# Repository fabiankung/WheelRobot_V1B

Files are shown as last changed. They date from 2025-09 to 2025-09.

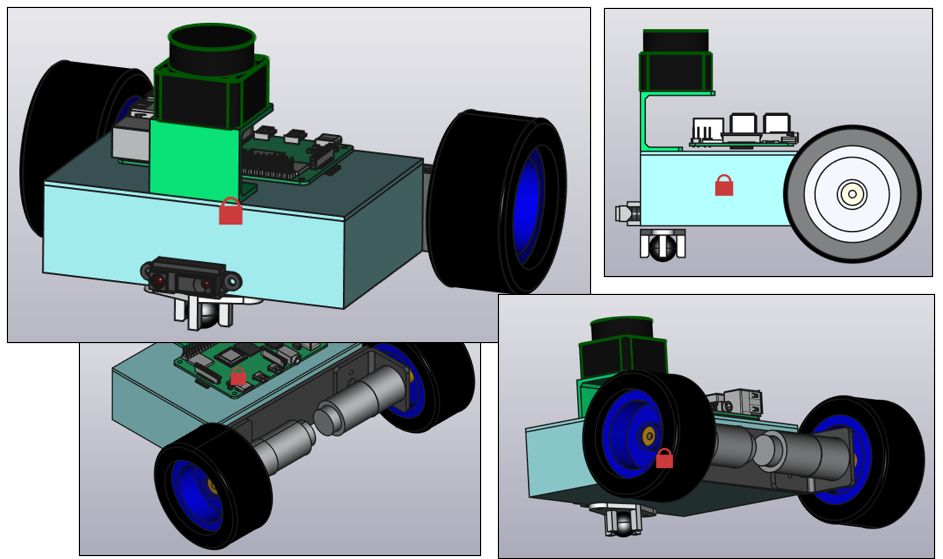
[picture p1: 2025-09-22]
WR1B.jpg

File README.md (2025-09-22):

# WheelRobot_V1B
A simple wheel robot using differential drive locomotion, with Raspberry Pi 4B single-board computer running ROS2 middleware for high-level control and monitoring. The robot has a custom low-level robot controller board using the chip dsPIC33CK512MP606 as the processor for controlling the DC motors and interfacing with on-board sensors. See the PDF file in this repo for the details of the low-level robot controller.

For videos of the robot in action, please see: https://youtu.be/-Cyti25GG1c

WR1B





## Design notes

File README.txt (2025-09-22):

The Sharp IR sensor CAD model is imported from STEP file, courtesy of DonLabs: https://grabcad.com/library/sharp-ir-sensor-gp2y0a41sk0f-1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,and%20also%20the%20data%20sheet%20for%20reference. 

The FreeCAD model for Raspberry Pi 4 is courtesy of rottengetter: https://forum.freecad.org/viewtopic.php?t=59273

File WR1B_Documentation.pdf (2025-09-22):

# CAD Design Using FreeCAD V1.0.0

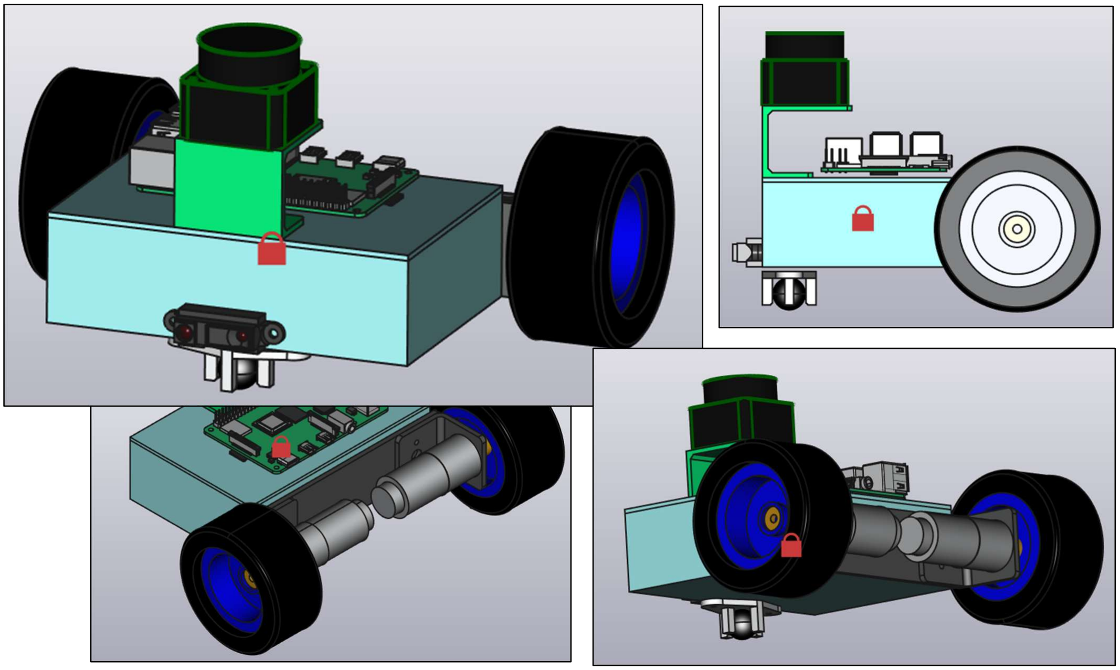
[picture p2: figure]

Wheel Robot Platform | 2025 by Fabian Kung Wai Lee | 1

# Wheel Robot Platform – WR1B

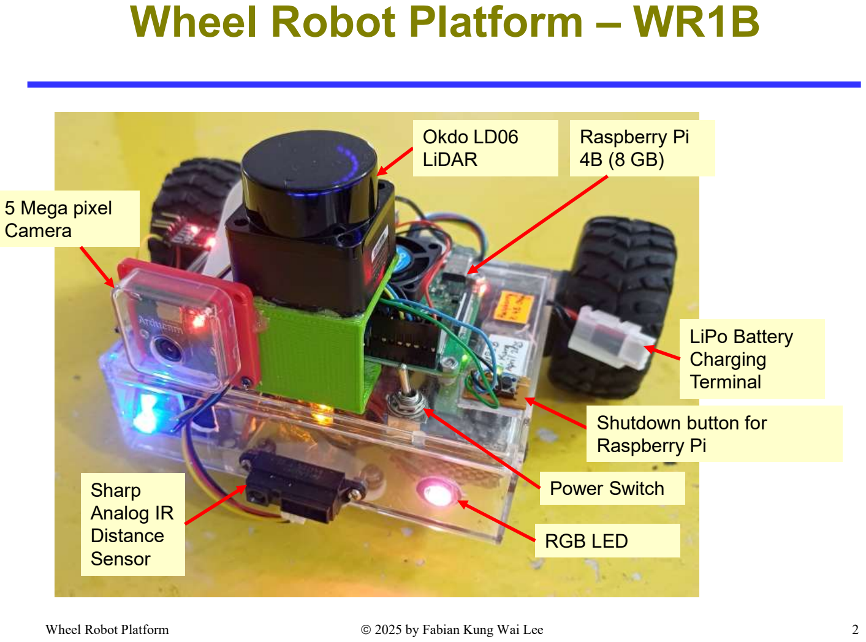
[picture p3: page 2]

Wheel Robot Platform | 2025 by Fabian Kung Wai Lee | 2

# Sharp Analog IR Distance Sensor

# Okdo LD06 LiDAR

# Raspberry Pi 4B (8 GB)

# 5 Mega pixel Camera

# RGB LED

# Power Switch

# LiPo Battery Charging Terminal

# Shutdown button for Raspberry Pi

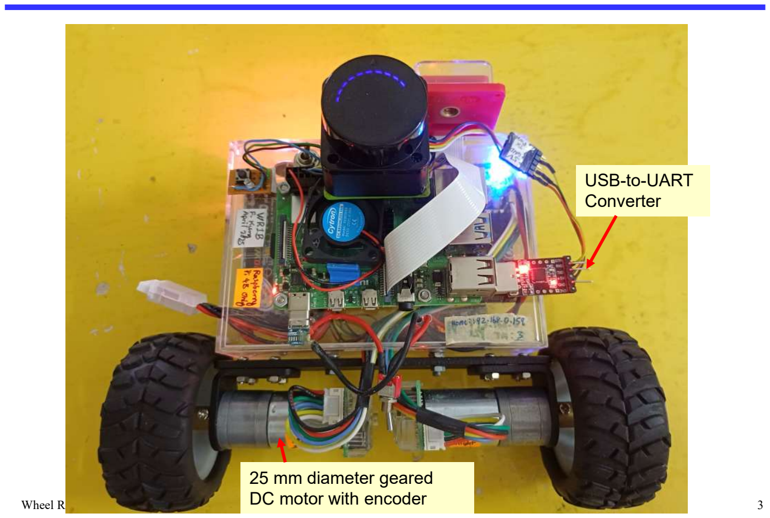
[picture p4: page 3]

Wheel Robot Platform | 2025 by Fabian Kung Wai Lee | 3

# 25 mm diameter geared DC motor with encoder

# USB-to-UART Converter

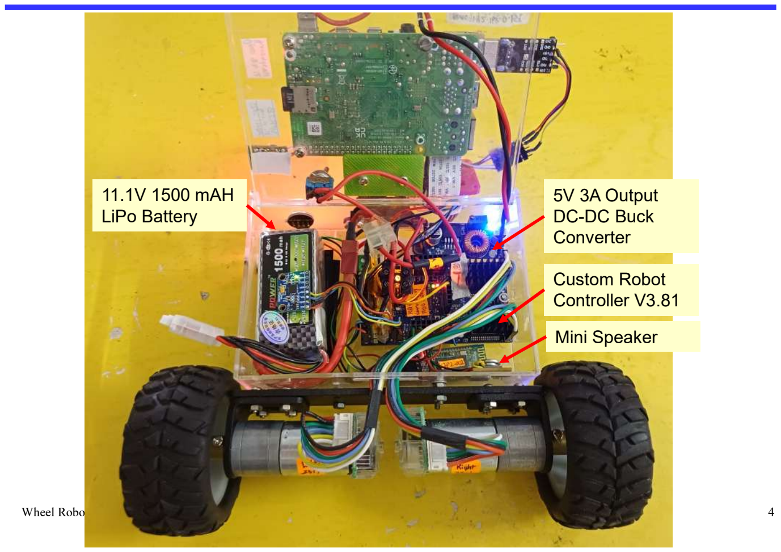
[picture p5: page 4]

Wheel Robot Platform | 2025 by Fabian Kung Wai Lee | 4

# 11.1V 1500 mAH LiPo Battery

# 5V 3A Output DC-DC Buck Converter

# Custom Robot Controller V3.81

# Mini Speaker

# Schematic of Robot Controller (V3.81) – MCU Core

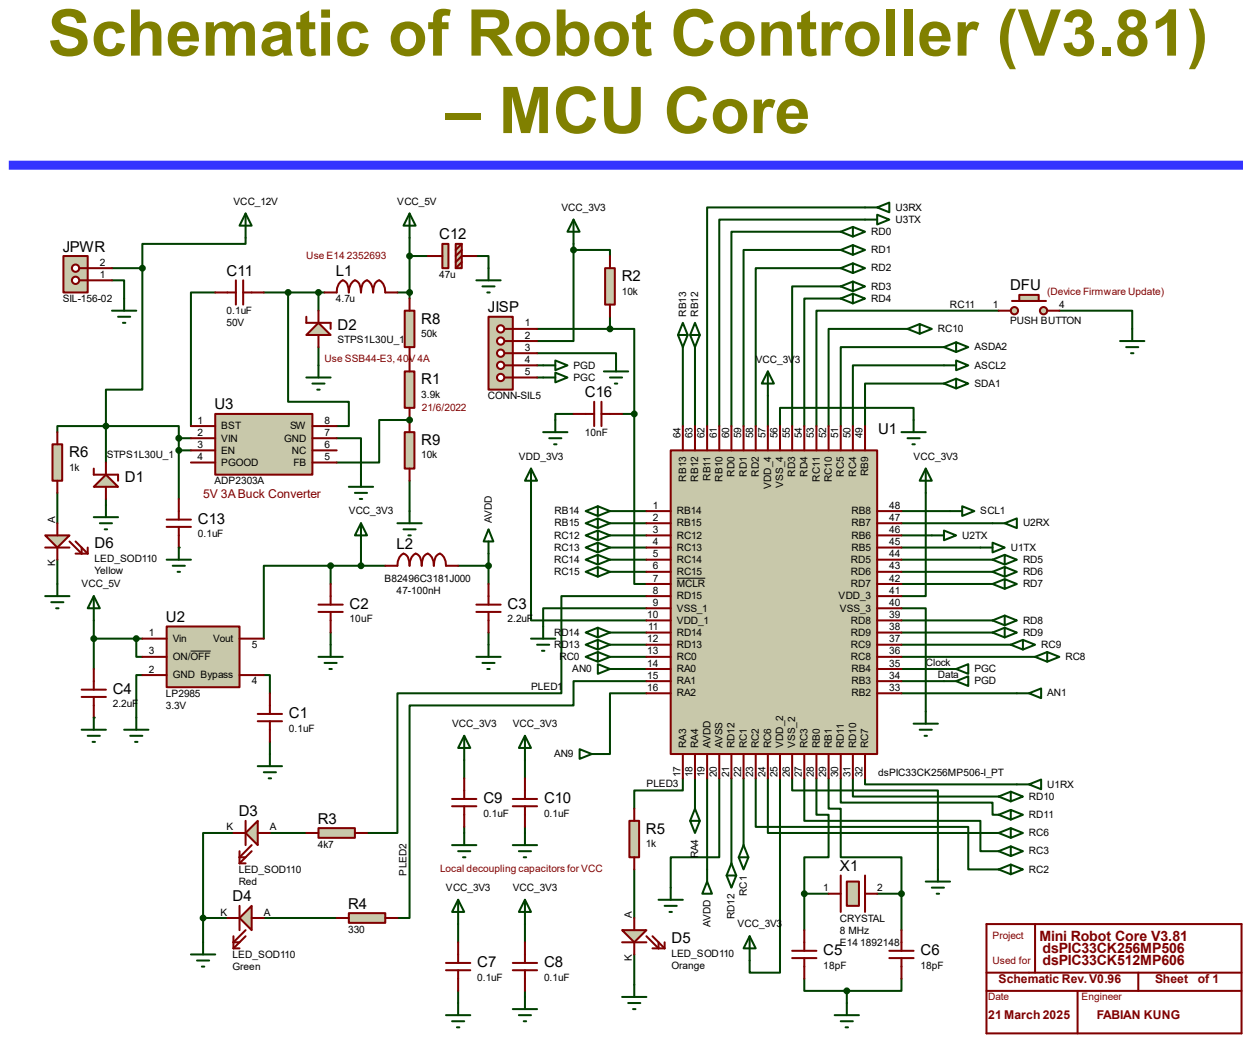
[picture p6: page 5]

Local decoupling capacitors for VCC
VCC_3V3

Project Used for | Mini Robot Core V3.81 dsPIC33CK512MP606 dsPIC33CK256MP506

Schematic Rev. V0.96 | Sheet of 1
Date 21 March 2025 | Engineer FABIAN KUNG

# Schematic of Robot Controller (V3.81) – I/O Ports Connections

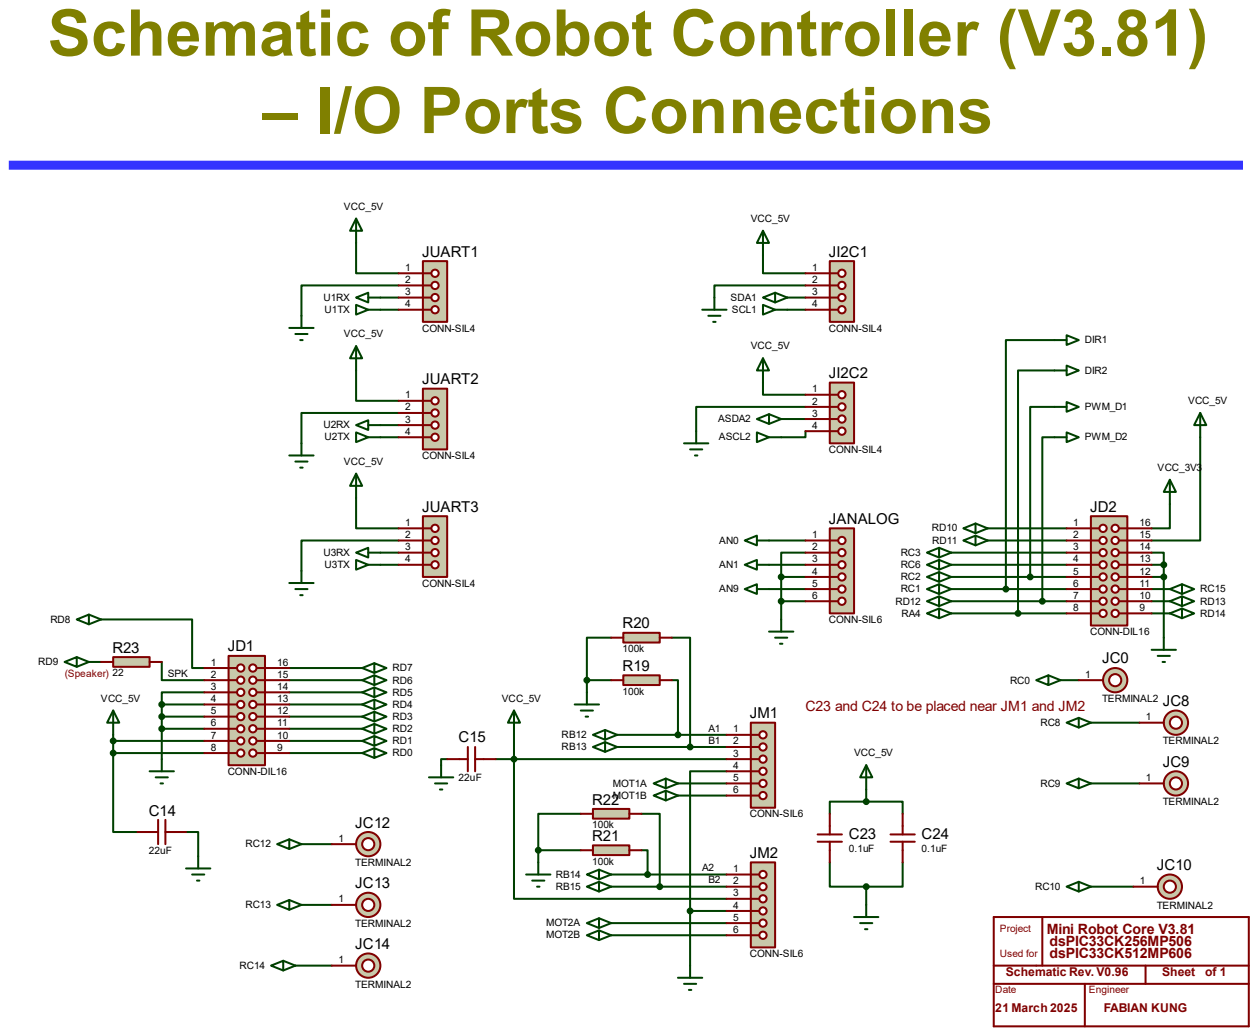
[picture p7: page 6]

C23 and C24 to be placed near JM1 and JM2

Project Used for | Mini Robot Core V3.81 dsPIC33CK512MP606 dsPIC33CK256MP506

Schematic Rev. V0.96 | Sheet of 1
Date 21 March 2025 | Engineer FABIAN KUNG

# Schematic of Robot Controller (V3.81) – Dual DC Motors Driver

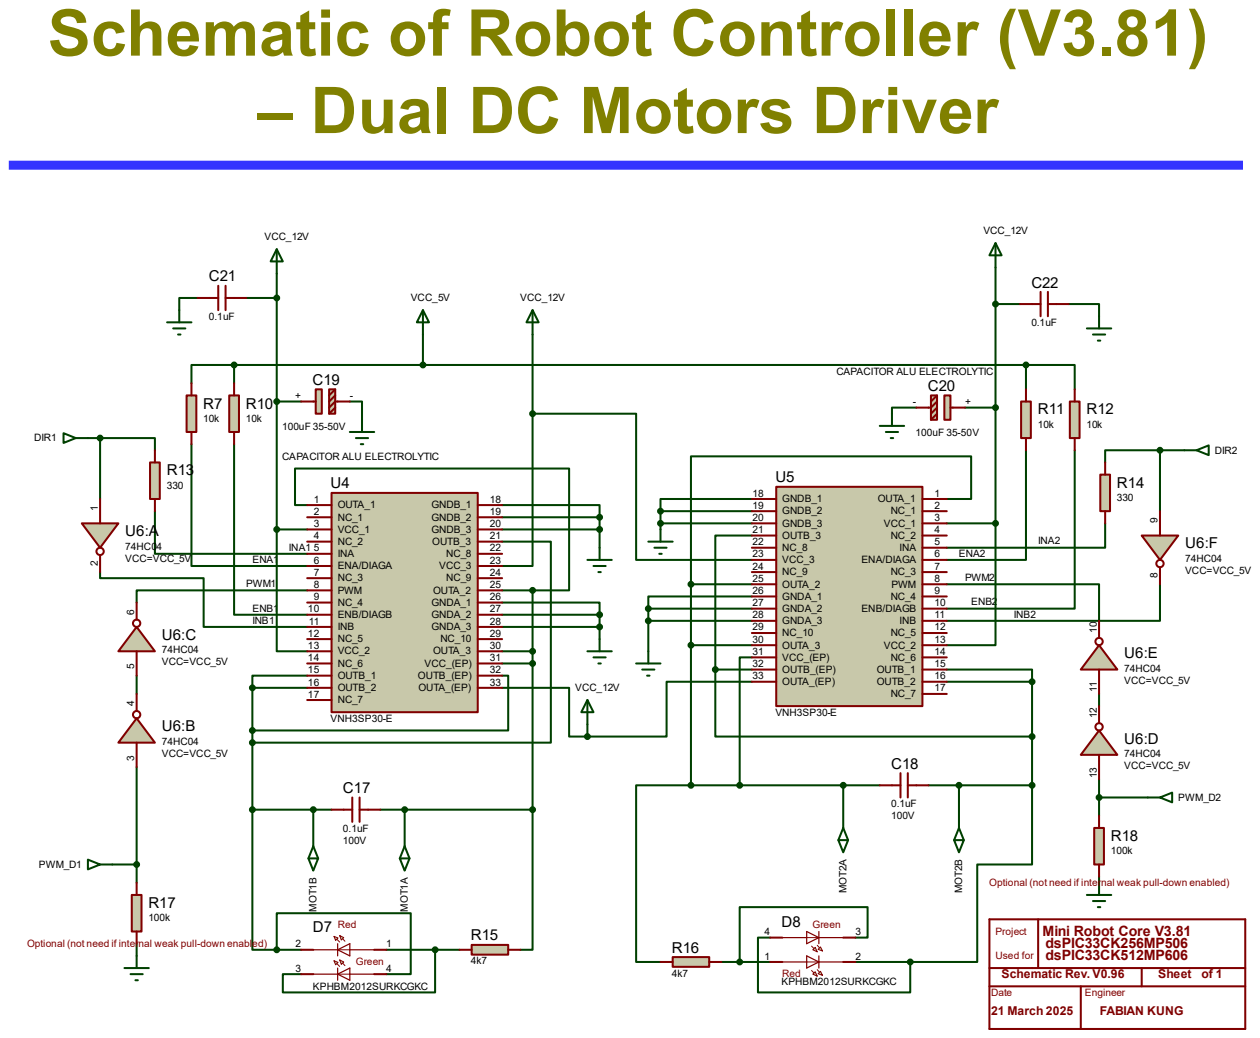
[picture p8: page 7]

100k Optional (not need if internal weak pull-down enabled)
PWM_D1

Optional (not need if internal weak pull-down enabled)

Project Used for | Mini Robot Core V3.81 dsPIC33CK512MP606 dsPIC33CK256MP506

Schematic Rev. V0.96 | Sheet of 1
Date 21 March 2025 | Engineer FABIAN KUNG

# PCB Artwork of Robot Controller

(V3.81)

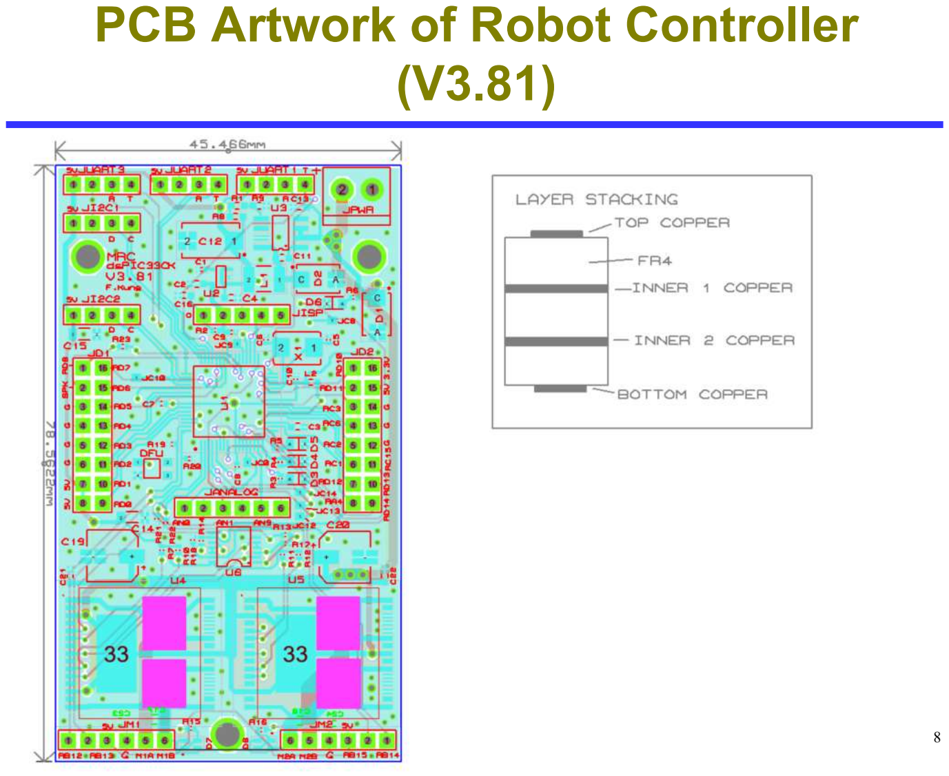
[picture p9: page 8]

Wheel Robot Platform | 2025 by Fabian Kung Wai Lee | 8

# Wiring Diagram

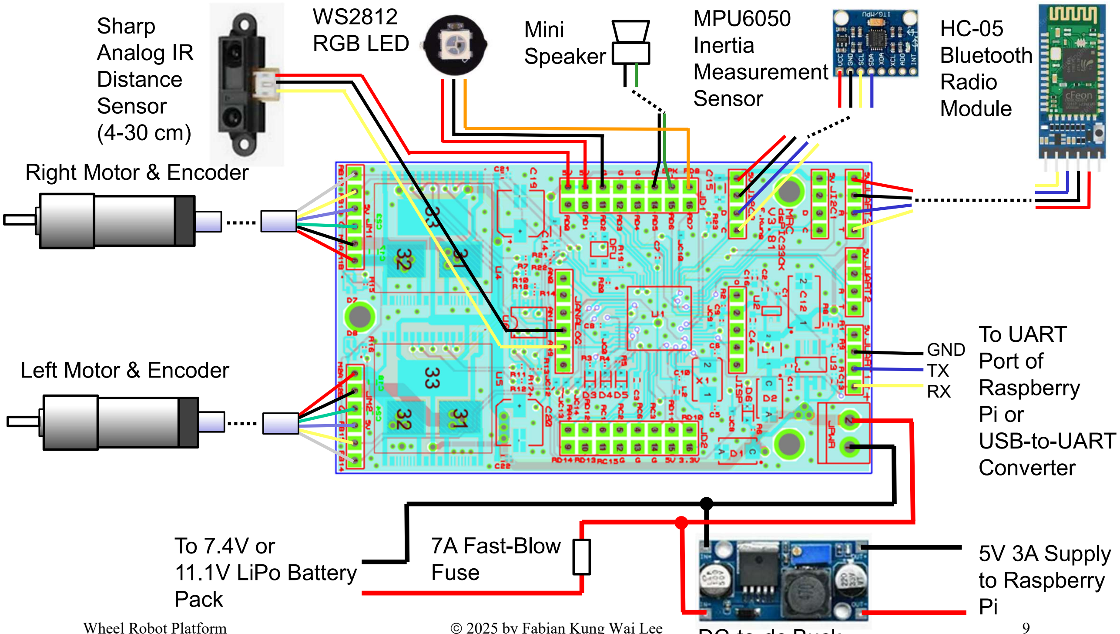
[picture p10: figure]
Right Motor & Encoder; Left Motor & Encoder; GND TX RX; HC-05 Bluetooth Radio Module; MPU6050 Inertia Measurement Sensor; To UART Port of Raspberry Pi or USB-to-UART Converter; To 7.4V or 11.1V LiPo Battery Pack; 5V 3A Supply to Raspberry Pi; 7A Fast-Blow Fuse; RGB LED; Mini; Speaker; Sharp Analog IR Distance Sensor (4-30 cm)

Wheel Robot Platform | 2025 by Fabian Kung Wai Lee | 9

# DC-to-dc Buck Converter

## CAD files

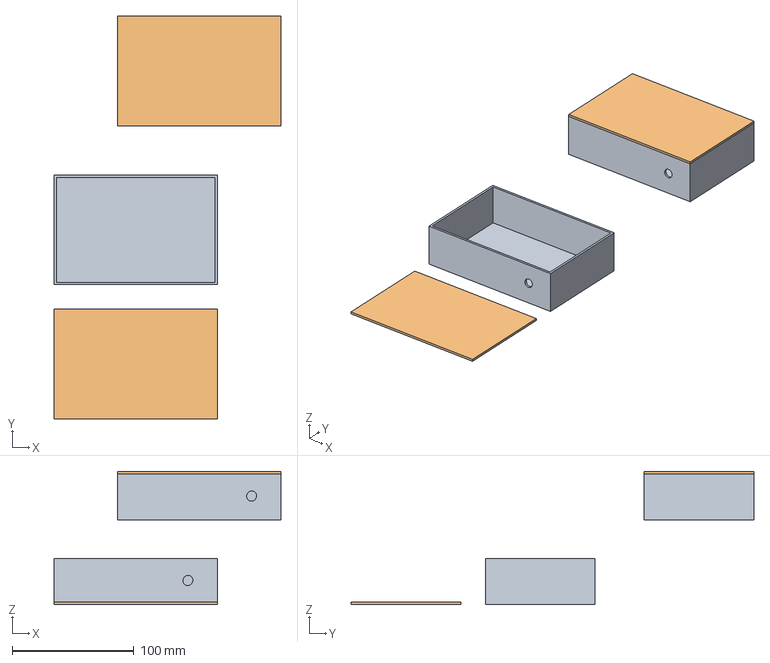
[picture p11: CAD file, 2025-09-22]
Mechanical_CAD/Main_Enclosure.FCStd
186.3 x 330.3 x 109.4 mm
Body_Bottom x 2
Body_Top x 2

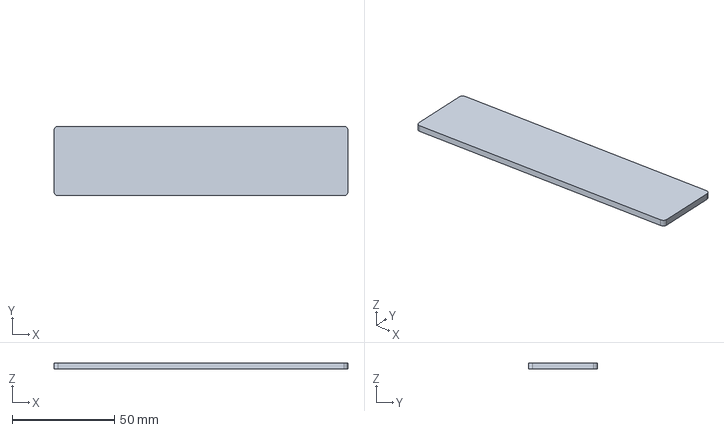
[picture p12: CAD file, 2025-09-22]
Mechanical_CAD/Motor_Sub_Assembly_Bracket.FCStd
144.0 x 34.0 x 3.00 mm

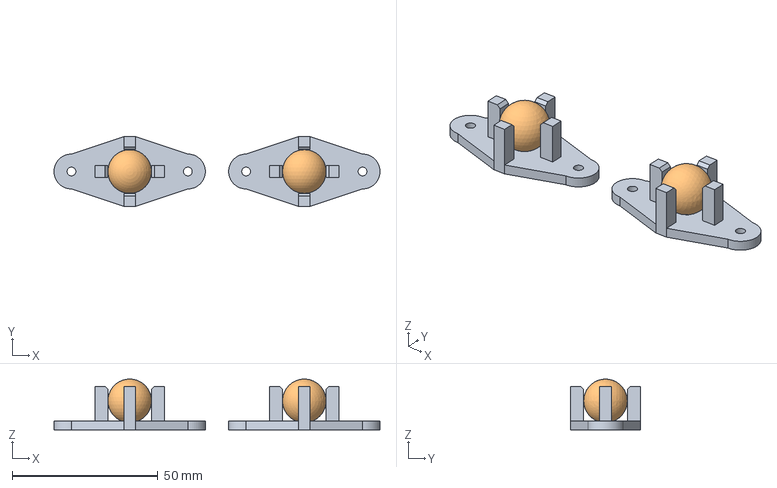
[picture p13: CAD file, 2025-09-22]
Mechanical_CAD/Castor_W420_Steel_Ball.FCStd
112.0 x 24.0 x 17.5 mm
Plastic_Bracket x 2
Steel_Ball x 2

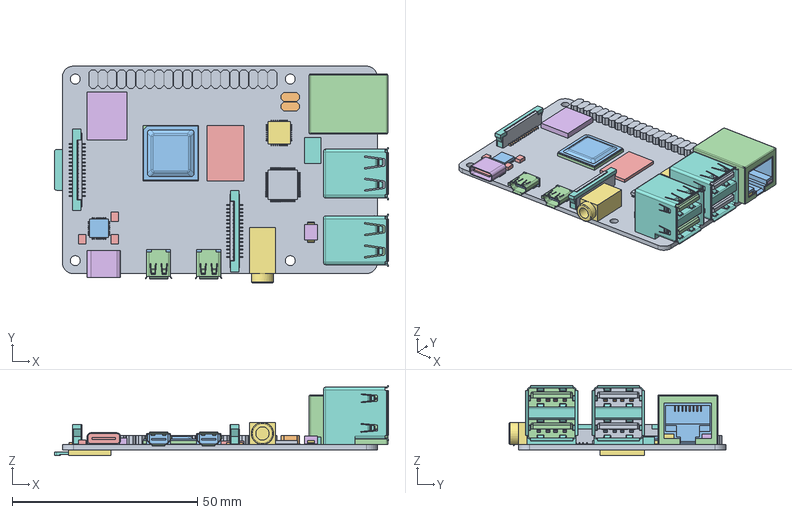
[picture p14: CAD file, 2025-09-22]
Mechanical_CAD/RaspPi-4B_rottengatter.FCStd
90.1 x 58.5 x 19.0 mm
PCB
Chip Carrier
Heat Spreader
Solder
RAM (LPDDR4)
Radio
Package x 3
Pins x 6
Inductor x 3
Capacitor
Shield x 6
Network Wires
LED (yellow)
LED (green)
Pin Carrier x 2
Pins (Upper Connector) x 2
Pins (Lower Connector) x 2
Phone Socket (Audio/Video)
Holder x 2
SD Card Slot
Contacts

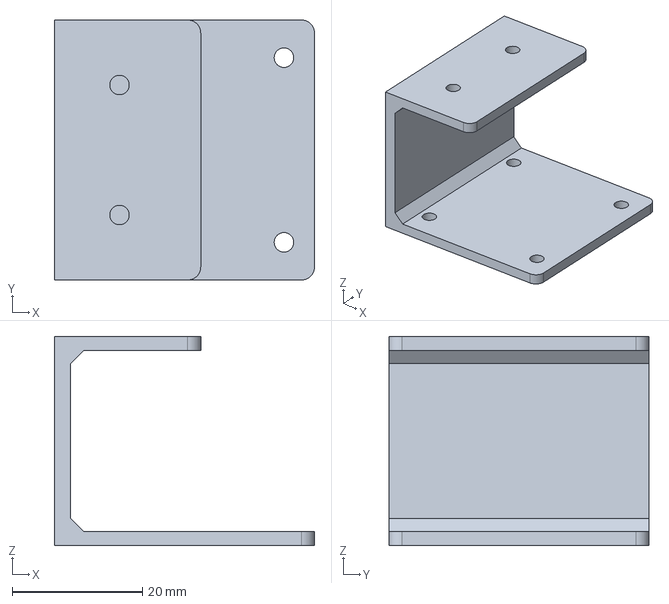
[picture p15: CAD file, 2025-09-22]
Mechanical_CAD/Lidar_Bracket.FCStd
40.0 x 40.0 x 32.2 mm

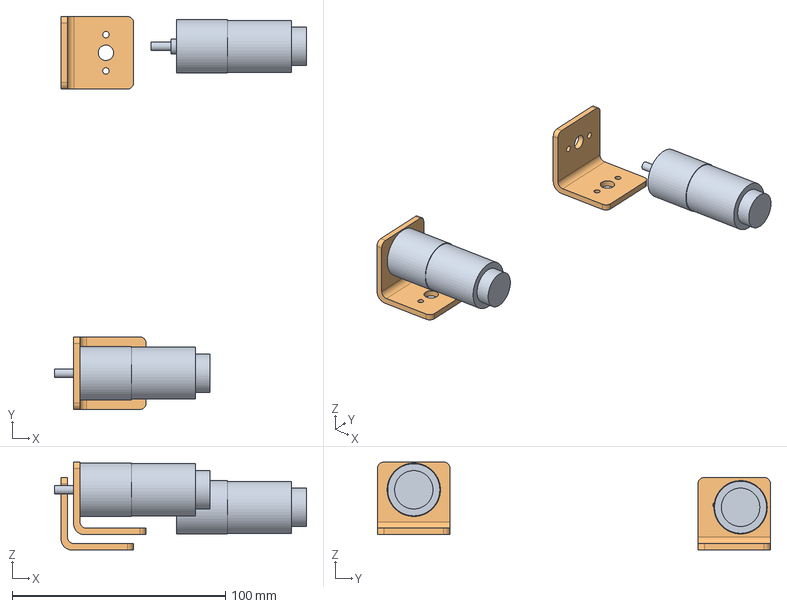
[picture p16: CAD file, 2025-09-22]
Mechanical_CAD/JGA25_DCMotor.FCStd
118.1 x 184.1 x 41.2 mm
Motor_Assembly x 2
Bracket x 2

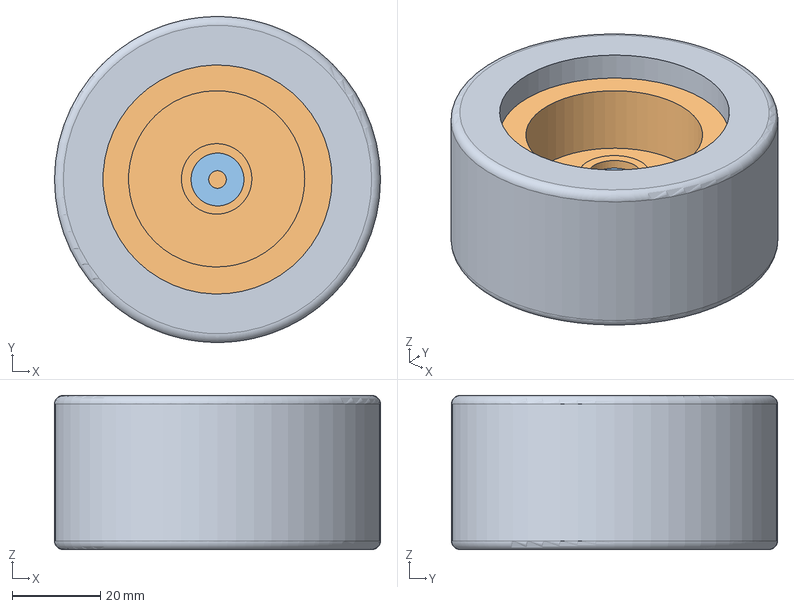
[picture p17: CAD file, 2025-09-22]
Mechanical_CAD/RubberWheel_75mm.FCStd
74.0 x 74.0 x 35.0 mm
Outer_Rubber
Rim
Coupler

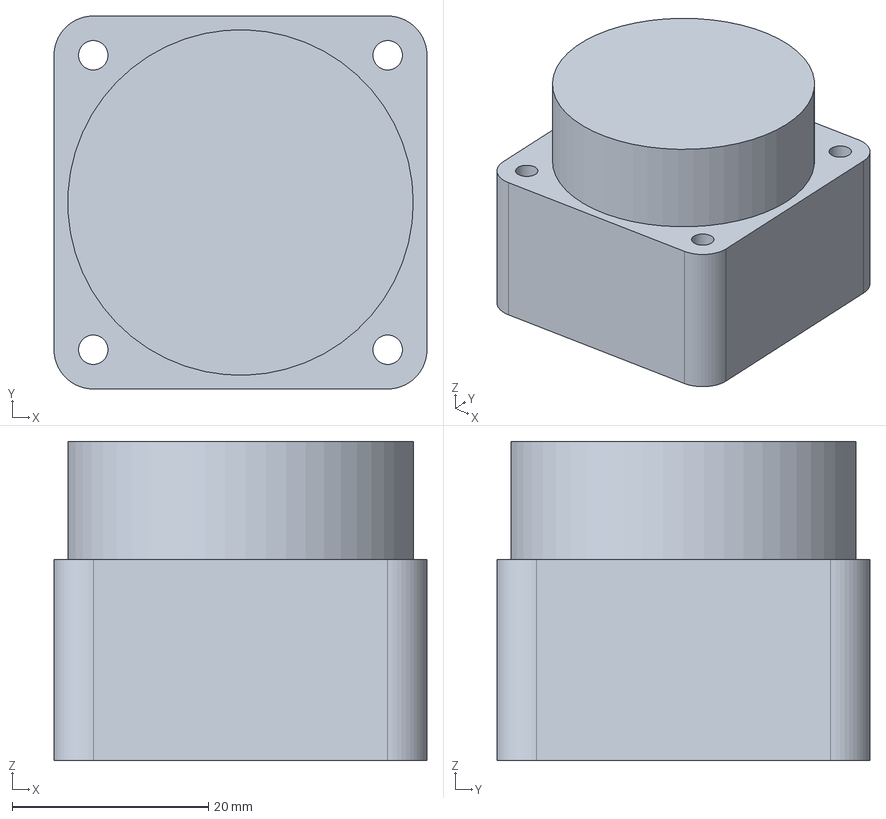
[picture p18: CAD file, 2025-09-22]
Mechanical_CAD/Lidar_Okdo_LD02.FCStd
38.0 x 38.0 x 32.5 mm

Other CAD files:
Mechanical_CAD/Assembly/WR1B.FCStd

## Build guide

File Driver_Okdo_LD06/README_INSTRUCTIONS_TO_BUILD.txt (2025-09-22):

1. Create a workspace in your home folder, say ros2_linolidar_ws.
2. Create a sub-folder /src in your workspace.
3. Copy the folder ldlidar into /src.
4. Goto your workspace in a terminal, i.e. /ros2_linolidar_ws
5. Build the project by running 'colcon build'

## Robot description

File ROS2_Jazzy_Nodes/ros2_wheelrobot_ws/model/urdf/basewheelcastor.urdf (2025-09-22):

<?xml version="1.0"?>
<robot name="fk_wheelrobot">

    <material name="grey">
        <color rgba="0.5 0.5 0.5 1" />
    </material>

    <material name="blue">
        <color rgba="0 0 0.5 1" />
    </material>
    
    <material name="lightgrey">
        <color rgba="0.8 0.8 0.8 1" />
    </material>    
    
    <material name="darkgrey">
        <color rgba="0.2 0.2 0.2 1" />
    </material>       
     
    <material name="white">
        <color rgba="1 1 1 1" />
    </material>      
    
    <!-- base_link (required for Nav2) -->
    <link name="base_link">
        <visual>
            <geometry>
                <box size="0.145 0.1 0.085" />
            </geometry>
            <origin xyz="0 0 0" rpy="0 0 0" />
            <material name="blue" />
        </visual>
    </link>
    
    <!-- base_footprint (projection of base_link on the ground) -->
    <!-- Required for Nav2 and Rviz2 -->
    <link name="base_footprint"/>   
    
    <joint name="base_joint" type="fixed">
        <parent link="base_footprint"/>
        <child link="base_link"/>
        <origin xyz="0 0 0.0645" rpy="0 0 0"/>
    </joint>    
     
    <!-- Wheels (2 differential wheels) -->

    <link name="left_wheel">
        <visual>
            <geometry>
                <cylinder radius="0.04" length="0.0385"/>
            </geometry>
            <origin xyz="0 0 0" rpy="1.57 0 0" />
            <material name="darkgrey" />
        </visual>
    </link>
    <joint name="base_left_wheel_joint" type="continuous">
        <parent link="base_link"/>
        <child link="left_wheel"/>
        <origin xyz="-0.0425 0.075 -0.0245" rpy="0 0 0"/>
        <axis xyz="0 1 0"/>
    </joint>
        
    <link name="right_wheel">
        <visual>
            <geometry>
                <cylinder radius="0.04" length="0.0385"/>
            </geometry>
            <origin xyz="0 0 0" rpy="1.57 0 0" />
            <material name="darkgrey" />
        </visual>
    </link>     
    <joint name="base_right_wheel_joint" type="continuous">
        <parent link="base_link"/>
        <child link="right_wheel"/>
        <origin xyz="-0.0425 -0.075 -0.0245" rpy="0 0 0"/>
        <axis xyz="0 1 0"/>
    </joint>
    
    <!-- Castor wheel to keep the balance -->
    <link name="caster_wheel">
        <visual>
            <geometry>
                <sphere radius="0.011"/>
            </geometry>
            <origin xyz="0 0 0" rpy="0 0 0" />
            <material name="white" />
        </visual>
    </link>  
    
    <joint name="base_caster_wheel_joint" type="fixed">
        <parent link="base_link"/>
        <child link="caster_wheel"/>
        <origin xyz="0.0525 0 -0.054" rpy="0 0 0"/>
    </joint>  
             
</robot>

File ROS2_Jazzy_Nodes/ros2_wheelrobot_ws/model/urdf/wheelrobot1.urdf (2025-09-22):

<?xml version="1.0"?>

<!-- Last modified 11 Aug 2025 -->
<!-- by Fabian Kung -->

<robot name="fk_wheelrobot" xmlns:xacro="http://ros.org/wiki/xacro">

    <material name="grey">
        <color rgba="0.5 0.5 0.5 1" />
    </material>

    <material name="blue">
        <color rgba="0 0 0.5 1" />
    </material>
    
    <material name="lightgrey">
        <color rgba="0.8 0.8 0.8 1" />
    </material>    
    
    <material name="darkgrey">
        <color rgba="0.2 0.2 0.2 1" />
    </material>       
     
    <material name="white">
        <color rgba="1 1 1 1" />
    </material> 
    
    <material name="yellow">
        <color rgba="1 1 0 1" />
    </material>      
    
    <!-- base_link (required for Nav2) -->
    <link name="base_link">
        <visual>
            <geometry>
                <box size="0.145 0.1 0.085" />
            </geometry>
            <origin xyz="0 0 0" rpy="0 0 0" />
            <material name="blue" />
        </visual>
    </link>
    
    <!-- base_footprint (projection of base_link on the ground) -->
    <!-- Required for Nav2 and Rviz2 -->
    <link name="base_footprint"/>   
    
    <joint name="base_joint" type="fixed">
        <parent link="base_footprint"/>
        <child link="base_link"/>
        <origin xyz="0 0 0.0645" rpy="0 0 0"/>
    </joint>    
     
   <!-- Top_body -->
    <link name="top_link">
        <visual>
            <geometry>
                <box size="0.132 0.160 0.028" />
            </geometry>
            <origin xyz="0 0 0" rpy="0 0 0" />
            <material name="blue" />
        </visual>
    </link>  
    
    <!-- The z offset is 0.5*(base_link.height + top_link.height)-->
    <joint name="base_top_joint" type="fixed">
        <parent link="base_link"/>
        <child link="top_link"/>
        <origin xyz="0 0 0.0565" rpy="0 0 0"/>
    </joint>          
     
    <!-- Wheels (2 differential wheels) -->
    <link name="left_wheel">
        <visual>
            <geometry>
                <cylinder radius="0.042" length="0.0385"/>
            </geometry>
            <origin xyz="0 0 0" rpy="1.57 0 0" />
            <material name="darkgrey" />
        </visual>
    </link>

    <joint name="base_left_wheel_joint" type="continuous">
        <parent link="base_link"/>
        <child link="left_wheel"/>
        <origin xyz="-0.0425 0.078 -0.0243" rpy="0 0 0"/>
        <axis xyz="0 1 0"/>
    </joint>
        
    <link name="right_wheel">
        <visual>
            <geometry>
                <cylinder radius="0.042" length="0.0385"/>
            </geometry>
            <origin xyz="0 0 0" rpy="1.57 0 0" />
            <material name="darkgrey" />
        </visual>
    </link>    

    <joint name="base_right_wheel_joint" type="continuous">
        <parent link="base_link"/>
        <child link="right_wheel"/>
        <origin xyz="-0.0425 -0.078 -0.0243" rpy="0 0 0"/>
        <axis xyz="0 1 0"/>
    </joint>
    
    <!-- Castor wheel to keep the balance -->
    <link name="caster_wheel">
        <visual>
            <geometry>
                <sphere radius="0.011"/>
            </geometry>
            <origin xyz="0 0 0" rpy="0 0 0" />
            <material name="white" />
        </visual>
    </link>  
    
    <joint name="base_caster_wheel_joint" type="fixed">
        <parent link="base_link"/>
        <child link="caster_wheel"/>
        <origin xyz="0.0525 0 -0.0540" rpy="0 0 0"/>
    </joint>  
             
    <!-- Various sensors link -->
    <!-- Lidar sensor (required for Nav2) -->
    <link name="base_laser">
        <visual>
            <geometry>
                <cylinder radius="0.017" length="0.012"/>
            </geometry>
            <origin xyz="0 0 0" rpy="0 0 0" />
            <material name="yellow" />
        </visual>
    </link>    
    
    <joint name="base_laser_joint" type="fixed">
        <parent link="base_link"/>
        <child link="base_laser"/>
        <origin xyz="0.0 0.0 0.1095" rpy="0 0 0"/>
        <axis xyz="0 0 1"/>    
    </joint>

    <!-- Range sensors link -->
    
    <link name="front_rsen_link">
        <visual>
            <geometry>
                <box size="0.014 0.03 0.013" />
            </geometry>
            <origin xyz="0 0 0" rpy="0 0 0" />
            <material name="yellow" />
        </visual>
    </link>   
    
    <joint name="front_rsen_joint" type="fixed">
        <parent link="base_link"/>
        <child link="front_rsen_link"/>
        <origin xyz="0.08 0.0 -0.03" rpy="0 0 0"/>
    </joint>    
    
</robot>

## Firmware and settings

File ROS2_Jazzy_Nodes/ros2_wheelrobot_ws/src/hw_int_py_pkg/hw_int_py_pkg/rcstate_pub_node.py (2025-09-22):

#!/usr/bin/env python3      # Only use python 3.
'''
Description:    Code to convert the raw robot controller raw state parameters
                into Navigation2 required messages, and publish these.
Author:         Fabian Kung
Last modified:  7 June 2025
'''

import rclpy                # Library for ROS2 in python. Note that this
                            # is a package, i.e. it is a folder named 
                            # 'rclpy' and contains a number of *.py 
                            # files which are the various modules making 
                            # up the library.
from rclpy.node import Node
from custom_robot_interface.msg import RCStateRaw
from sensor_msgs.msg import Range
from sensor_msgs.msg import JointState
from nav_msgs.msg import Odometry
#from geometry_msgs.msg import Point, Pose, Quaternion, Twist, Vector3
from geometry_msgs.msg import TransformStamped
from tf2_ros import TransformBroadcaster
from math import cos, sin

#import robot_physical_params as robot

# Declare constants of wheel robot platform
_RC_OS_TICK_SECONDS = 0.0001667
_NO_TICK_ROTATION = 382.0
_RAD_PER_TICK = 6.2832/_NO_TICK_ROTATION # 2*pi/(num_tick_rotation)

class RCStatePubNode(Node):  # Create a class, inherited from the Node class.

    # Static variables in the class.
    ranger_msg = Range()    # Object for storing IR range sensor data, right.
    rangel_msg = Range()    # Object for storing IR range sensor data, left.
    rangef_msg = Range()    # Object for storing IR range sensor data, front.
    jointstate_msg = JointState() # Object for storing joint state data.
    odom_msg = Odometry()   # Object for storing odometry information (from wheel encoders).
    tfodombase = TransformStamped() # Object for storing transform (tf) data, odom-->base_footprint mapping.

    dw = 0.184  # Wheel pitch, meter, this needs to tally with robot model in URDF file.
    rw = 0.037  # Wheel radius, meter, this needs to tally with robot model in URDF file.
    rw_dw = rw/dw
    rw_2 = rw/2.0

    def __init__(self):     # Constructor.
        super().__init__("rcstate_pub_node") # Create a node, initialize node name. 
                            # Basically here we run all the parent's constructors. 
                            # In python, the super() function is used to give
                            # access to methods and properties of a parent or
                            # sibling class.  
        self.get_logger().info("RC State Publisher node starting up...")

        # Create a publisher using the interface odom_msgs.msg.Odometry.
        self.publisher_odom = self.create_publisher(Odometry, "odom", 10)

        # Create a publisher using the interface sensor_msgs.msg.JointState.
        self.publisher_jointstate = self.create_publisher(JointState, "joint_states", 10)

        # Create a subscriber using the interface RCStateRaw, with topic "t_rc_status"
        # and queue size of 8.                    
        self.subscriber_ = self.create_subscription(RCStateRaw, 
                                                    "t_rc_status",self.Subscriber_Callback,10)
        
        # Create a tf transform broadcaster for TransformStamped.
        self.tf_broadcaster = TransformBroadcaster(self)

        # Setup constant parameters of Jointstate message:
        self.jointstate_msg.header.frame_id = ""    # Leave it empty, follow joint_state_publisher_gui package.
        self.jointstate_msg.name = ['base_left_wheel_joint','base_right_wheel_joint']
        
        # Setup constant parameters of Odometry message:
        self.odom_msg.header.frame_id = 'odom'
        self.odom_msg.child_frame_id = 'base_footprint'      
        self.odom_msg.pose.covariance = [
            0.1, 0.0, 0.0, 0.0, 0.0, 0.0,   # Probably we can set all off-diagonal elements to zero.
            0.0, 0.1, 0.0, 0.0, 0.0, 0.0,   # The diagonal elements is the variance associated with
            0.0, 0.0, 0.1, 0.0, 0.0, 0.0,   # each variable.    
            0.0, 0.0, 0.0, 0.1, 0.0, 0.0,
            0.0, 0.0, 0.0, 0.0, 0.1, 0.0,
            0.0, 0.0, 0.0, 0.0, 0.0, 0.1
        ]
        self.odom_msg.twist.covariance = [
            0.1, 0.0, 0.0, 0.0, 0.0, 0.0,
            0.0, 0.1, 0.0, 0.0, 0.0, 0.0,
            0.0, 0.0, 0.1, 0.0, 0.0, 0.0,
            0.0, 0.0, 0.0, 0.1, 0.0, 0.0,
            0.0, 0.0, 0.0, 0.0, 0.1, 0.0,
            0.0, 0.0, 0.0, 0.0, 0.0, 0.1
        ]

        # Setup constant parameters of TF message:
        self.tfodombase.header.frame_id = "odom"
        self.tfodombase.child_frame_id = 'base_footprint'
        
        # Initial wheel angles or count.
        self.wrotationr = 0     # Wheel count
        self.wrotationl = 0
        self.wthetar = 0.0      # Wheel angle
        self.wthetal = 0.0
        # Initial pose and time.
        self.x = 0.0
        self.y = 0.0
        self.theta = 0.0
        self.lasttimestamp = 0
        

    # Subscriber callback function, publish range sensor data
    def Subscriber_Callback(self, msg):

        #self.get_logger().info("Raw state received")        
        timestamp = self.get_clock().now()      # Get current time-stamp in nano seconds.
        timestamp_msg = timestamp.to_msg()      # Convert time-stamp to message.

        self.jointstate_msg.header.stamp = timestamp_msg

        self.odom_msg.header.stamp = timestamp_msg

        self.tfodombase.header.stamp = timestamp_msg

        # Calculate time interval since last message.
        dt = (msg.timestamp - self.lasttimestamp)*_RC_OS_TICK_SECONDS 
        self.lasttimestamp = msg.timestamp # Update current timestamp.
        #self.get_logger().info("dt in sec " + str(dt))
        
        wcoeff = _RAD_PER_TICK / dt
        # Update estimated wheel angles. The reported values from robot controller (RC) is
        # number of wheel encoder ticks.
        self.wthetar = msg.rotater * _RAD_PER_TICK 
        self.wthetal = msg.rotatel * _RAD_PER_TICK   
        # Estimate the wheel angular velocity in rad/sec from change in wheel rotation count.
        wr = (msg.rotater - self.wrotationr)*wcoeff 
        wl = (msg.rotatel - self.wrotationl)*wcoeff 
        self.wrotationl = msg.rotatel # Update current rotation count for left wheel.
        self.wrotationr = msg.rotater # Update current rotation count for right wheel.

        # Calculate v and w from wheel angular velocities.
        v = (self.rw_2)*(wr + wl)           # 
        w = (self.rw_dw)*(wr - wl)
    
        # Updating the estimated pose of the robot using finite difference, based on the 
        # kinematic formulation by S. Thrun et-al, "Probabilistic robotics", 2005, MIT Press.
        dtheta = w * dt
        theta_new = self.theta + dtheta

        if (dtheta < 0.01):             # Use straight line approximation when angular velocity
                                        # is too small.
            Vdt = v*dt
            dx = Vdt*cos(self.theta)
            dy = Vdt*sin(self.theta)        
        else:                           # General curvilinear motion where robot move and turn 
                                        # at the same time.
            R = v/w
            dx = R*(-sin(self.theta)+sin(theta_new))
            dy = R*(cos(self.theta) - cos(theta_new))

        self.x = self.x + dx
        self.y = self.y + dy
        self.theta = theta_new
        
   
        # Debug messages
        #self.get_logger().info("wr " + str(wr))
        #self.get_logger().info("wl " + str(wl))
        #self.get_logger().info("v in rps " + str(v/(self.rw*6.283)))
        #self.get_logger().info("v in m/s " + str(v))
        #self.get_logger().info("w in rad/s" + str(w))  
        #self.get_logger().info("th " + str(self.theta)) 
        #self.get_logger().info("x " + str(self.x))
        #self.get_logger().info("y " + str(self.y)) 
        #self.get_logger().info("wthetar " + str(self.wthetar))
        #self.get_logger().info("wthetal " + str(self.wthetal))
        #self.get_logger().info("odometry x=" + str(self.x) + " y=" + str(self.y) + " z=" + str(0.0))

        '''
        Set the pose, in (x,y,z) and unit quarternion (x,y,z,w).
        Unit quarternion is a compact way to hold the rotation
        information in equivalent angle-axis representation (J. Craig, "Introduction
        to robotics - mechanics and control", 4th edition 2022, Pearson). The equi-
        valent axis is a unit vector. Assuming axis = kx*i+ky*j+kz*k, where i,j and k
        are the unit vectors along x,y and z axis, and angle = theta, then the unit
        quarternion elements are given by:
        x = kx*sin(theta/2)
        y = ky*sin(theta/2)
        z = kz*sin(theta/2)
        w = cos(theta/2)

        For our robot, axis = 0*i+0*j+1*k  (Rotation along z-axis)
        angle = theta_new, thus q = (x,y,z,w) is:
        x = 0
        y = 0
        z = sin(theta_new/2)
        w = cos(theta_new/2)
        '''
        self.odom_msg.pose.pose.position.x = self.x
        self.odom_msg.pose.pose.position.y = self.y
        self.odom_msg.pose.pose.position.z = 0.0
        self.odom_msg.pose.pose.orientation.x = 0.0  # Orientation is in quarternion format.
        self.odom_msg.pose.pose.orientation.y = 0.0
        self.odom_msg.pose.pose.orientation.z = sin(theta_new/2.0)
        self.odom_msg.pose.pose.orientation.w = cos(theta_new/2.0)

        self.tfodombase.transform.translation.x = self.x
        self.tfodombase.transform.translation.y = self.y
        self.tfodombase.transform.translation.z = 0.0
        self.tfodombase.transform.rotation.x = 0.0
        self.tfodombase.transform.rotation.y = 0.0
        self.tfodombase.transform.rotation.z = sin(theta_new/2.0)
        self.tfodombase.transform.rotation.w = cos(theta_new/2.0)

        # Set the twist.
        self.odom_msg.twist.twist.linear.x = v*cos(theta_new/2.0)
        self.odom_msg.twist.twist.linear.y = v*sin(theta_new/2.0)
        self.odom_msg.twist.twist.linear.z = 0.0
        self.odom_msg.twist.twist.angular.z = w

        # Set all joint states.
        self.jointstate_msg.position = [self.wthetal, self.wthetar]
        self.publisher_jointstate.publish(self.jointstate_msg)  # Publish joint state message.
        self.publisher_odom.publish(self.odom_msg)      # Publish odometry message.
        
        self.tf_broadcaster.sendTransform(self.tfodombase)


def main(args=None):
    rclpy.init(args=args)   # Initialize ROS communication library.
    node = RCStatePubNode()  # Instantiate class.
    rclpy.spin(node)        # Block the current node so that other process can run.
    rclpy.shutdown()        # Shutdown.

if __name__ == "__main__":  # Only run this part if this file (or module as python file
                            # is called) is invoked directly by the python intepreter.
    main()

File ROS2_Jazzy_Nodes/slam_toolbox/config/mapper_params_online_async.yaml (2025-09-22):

slam_toolbox:
  ros__parameters:

    # Plugin params
    solver_plugin: solver_plugins::CeresSolver
    ceres_linear_solver: SPARSE_NORMAL_CHOLESKY
    ceres_preconditioner: SCHUR_JACOBI
    ceres_trust_strategy: LEVENBERG_MARQUARDT
    ceres_dogleg_type: TRADITIONAL_DOGLEG
    ceres_loss_function: None

    # ROS Parameters
    odom_frame: odom
    map_frame: map
    base_frame: base_footprint
    scan_topic: /scan
    use_map_saver: true
    mode: mapping #localization

    # if you'd like to immediately start continuing a map at a given pose
    # or at the dock, but they are mutually exclusive, if pose is given
    # will use pose
    #map_file_name: test_steve
    # map_start_pose: [0.0, 0.0, 0.0]
    #map_start_at_dock: true

    debug_logging: false
    throttle_scans: 1
    transform_publish_period: 0.025 #if 0 never publishes odometry. Need to tally with actual /tf message from robot hardware.
    map_update_interval: 5.0
    resolution: 0.05
    max_laser_range: 12.0 #for rastering images, need to tally with the actual Lidar used.
    minimum_time_interval: 0.5
    transform_timeout: 0.2
    tf_buffer_duration: 30.
    #stack_size_to_use: 40000000 # program needs a larger stack size to serialize large maps, 4MByte default.
    stack_size_to_use: 160000000  # Larger stack size for larger area.
    enable_interactive_mode: true

    # General Parameters
    use_scan_matching: true
    use_scan_barycenter: true
    minimum_travel_distance: 0.5
    minimum_travel_heading: 0.5
    scan_buffer_size: 10
    scan_buffer_maximum_scan_distance: 10.0
    link_match_minimum_response_fine: 0.1  
    link_scan_maximum_distance: 1.5
    loop_search_maximum_distance: 3.0
    do_loop_closing: true 
    loop_match_minimum_chain_size: 10           
    loop_match_maximum_variance_coarse: 3.0  
    loop_match_minimum_response_coarse: 0.35    
    loop_match_minimum_response_fine: 0.45

    # Correlation Parameters - Correlation Parameters
    correlation_search_space_dimension: 0.5
    correlation_search_space_resolution: 0.01
    correlation_search_space_smear_deviation: 0.1 

    # Correlation Parameters - Loop Closure Parameters
    loop_search_space_dimension: 8.0
    loop_search_space_resolution: 0.05
    loop_search_space_smear_deviation: 0.03

    # Scan Matcher Parameters
    distance_variance_penalty: 0.5      
    angle_variance_penalty: 1.0    

    fine_search_angle_offset: 0.00349     
    coarse_search_angle_offset: 0.349   
    coarse_angle_resolution: 0.0349        
    minimum_angle_penalty: 0.9
    minimum_distance_penalty: 0.5
    use_response_expansion: true

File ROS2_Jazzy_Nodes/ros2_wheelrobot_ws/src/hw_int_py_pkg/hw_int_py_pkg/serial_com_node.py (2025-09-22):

#!/usr/bin/env python3      # Only use python 3.
'''
Description:    Code to handle outgoing and incoming data packets from
                serial port (to physical robot platform)
Author:         Fabian Kung
Last modified:  16 Aug 2025

Last modification: Instead of using USB-to-serial converter, I enabled
the build-in UART port in Raspberry Pi connected to GPIO14 and GPIO15.
Will be using this UART port to communicate with low-level Robot 
Controller module.
'''

import rclpy                # Library for ROS2 in python. Note that this
                            # is a package, i.e. it is a folder named 
                            # 'rclpy' and contains a number of *.py 
                            # files which are the various modules making 
                            # up the library.
from rclpy.node import Node

from custom_robot_interface.msg import RCStateRaw
from geometry_msgs.msg import Twist # Import String datatype for messaging.
import serial

_LENGTH_OF_RX_PACKET = 22

class SerialComNode(Node):  # Create a class, inherited from the Node class.

    ReadData = []           # Class level variable, captured data from serial port.
    CurrentTimestamp = 0    # Initialize current time stamp.
    TimeStamp = 0
    Counter = 0

    def __init__(self):     # Constructor.
        super().__init__("serial_com_node") # Create a node, initialize node name. 
                            # Basically here we run all the parent's constructors. 
                            # In python, the super() function is used to give
                            # access to methods and properties of a parent or
                            # sibling class.
        #self.counter = 0    
        self.get_logger().info("Serial COM node starting up...")
        
        # Create a publisher using the interface RCStateRaw,
        # with topic name "t_rc_status", and queue size of 10.
        self.publisher_ = self.create_publisher(RCStateRaw, "t_rc_status", 10)

        # Create a subscriber using the interface Twist, with topic name 
        # "cmd_vel" and queue size of 10.                    
        self.subscriber_ = self.create_subscription(Twist, 
                                                    "cmd_vel",self.Subscriber_Callback,10)

        # Variables for Robot Controller (RC) serial interface.
        #self.RC_TX_Busy = False         # TX busy flag. Set to 'true' to
                                        # initiate sending of command to RC.
        #self.utf8TXCommandString = ""   # Command string to send to RC.
        #self.TXCount = 0                # TX count.

        # Create a timer
        # Timer period = 50 msec. This is sufficient for RC reporting rate of 3-6 Hz.
	# For higher update rate, we should use smaller duration. Experiment shows 
	# that 20 msec can support up to 20 Hz RC reporting rate.
        self.create_timer(0.01,self.Timer_Callback)
        
        # Create a serial port handle. Settings:
        # Baud rate = 38400 (for Arduino)
        #             115200 (for custom robotic controller)
        # Stop bit = 1
        # Parity = None
        # Byte length = 8 bits
        # Read timeout = 10 msec. External hardware usually responds
        # within 5 msec.
        # Write timeout = 10 msec. 
        #self.sport = serial.Serial('/dev/RCusb', 115200) # USB-to-serial converter.
        self.sport = serial.Serial('/dev/ttyS0', 115200) # Internal UART port.
        self.sport.timeout = 0.01 # Read timeout.
        self.sport.write_timeout = 0.01 # Write timeout.
        self.sport.reset_input_buffer() # Clear receive buffer first.

    """
    Callback function for timer, 
    This function contains routines to read data packet from external Robot Controller (RC).
    There are two kinds of data packets:
    1. Periodic RC status packet which report the hardware status of the robotic platform
       with format like this:
       Byte  Content
       0     'b'
       1      Timestamp.0 - Bits 7-0.
       2      Timestamp.1 - Bits 15-8. 
       3      Timestamp.2 - Bits 23-16.
       4      Timestamp.3 - Bits 31-24.
       5      Rotater.0 - Bits 7-0. 
       6      Rotater.1 - Bits 15-8.
       7      Rotater.2 - Bits 23-16.
       8      Rotater.3 - Bits 31-24.
       9      Rotatel.0 - Bts 7-0. 
       10     Rotatel.1 - Bits 15-8.
       11     Rotatel.2 - Bits 23-16.
       12     Rotatel.3 - Bits 31-24.
       13     Hardware status flags - Reserved
       14     Hardware status flags - Reserved      
       15     Sensor1.0 -  bits 7-0 
       16     Sensor1.1 -  bits 15-8 
       17     Sensor2.0 -  bits 7-0 
       18     Sensor2.1 -  bits 15-8
       19     Sensor3.0 -  bits 7-0
       20     Sensor3.1 -  bits 15-8
       21     Checksum byte, using sum complement method.

    2. Acknowledgement from RC when receiving a command packet from ROS2. This is just 1 byte,
       either ACK or NAK. (Not implementing for now)
    """
    def Timer_Callback(self):   

        if self.sport.is_open == True:
            bytetoread = self.sport.in_waiting
            if bytetoread > (_LENGTH_OF_RX_PACKET-1):  # At least 22 bytes
                #self.get_logger().info("Byte to read " + str(bytetoread))
                ReadData = self.sport.read(bytetoread)               
                self.sport.reset_input_buffer()
                #self.get_logger().info(str(ReadData))  # Echo receive data to terminal.
                    
                # Verify that the checksum value is correct. 
                # Here we are using the sum complement method, So all the bytes in the
                # received buffer should adds up to 256 (lower 8-bits is 0) or 0.
                sum = 0
                for data in ReadData:
                    sum = sum + data
                sum = sum & 0x00FF      # Mask out all bits except lower byte.
                #self.get_logger().info("Check sum " + str(sum))
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
